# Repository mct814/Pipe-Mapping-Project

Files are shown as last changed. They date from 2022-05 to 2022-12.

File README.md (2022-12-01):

# Pipe-Mapping-Project

## Executive Summary
The problem that we wish to solve is a simple one. Underground PVC piping is often necessary to fix but difficult to locate. Methods currently exist for the detection of large industrial pipes, but there is a distinct lack of such technology for small, residential PVC
pipes. This project proposes a new way of mapping pipe networks by using a small probe to record positional data
while harmlessly traversing the pipe. The team’s objective is to create a probe based system to traverse and map variable sized underground pipe networks in 3D space, within an acceptable margin of error. While developing a mechanical pipe traversal method for the probe is part of this project, the primary goal consists of setting up the base technology for 3D mapping and real time information collection inside of 2"-4" PVC pipe.

## Current Version Capabilities
The current version of our design is still in the testing phase. While we have developed a functional testing system including a probe casing, pulley system and PVC network our current probe cannot fit inside the PVC pipe. The probe is using an arduino nano to pole data points and connect to the laptop which runs the mapping software. This probe can collect data while being powered by a set of 3 AA batteries and transmit said data to the PC. We have designed an improved system that would fit inside the 2" pipe but we have not yet implemented it. Our current mapping software can get data points within a relativiely similar shape to the physical path but still has a large margin of error. Further develpment of the mapping software is required to get within our original specification of 1" margin of error.

## Salient Outcomes
Our main successes came in the form of the mechanical testing system shown below and the preliminary maps created during testing.
* [Mechanical Testing](https://youtube.com/shorts/g99_hG3kM2Y?feature=share)

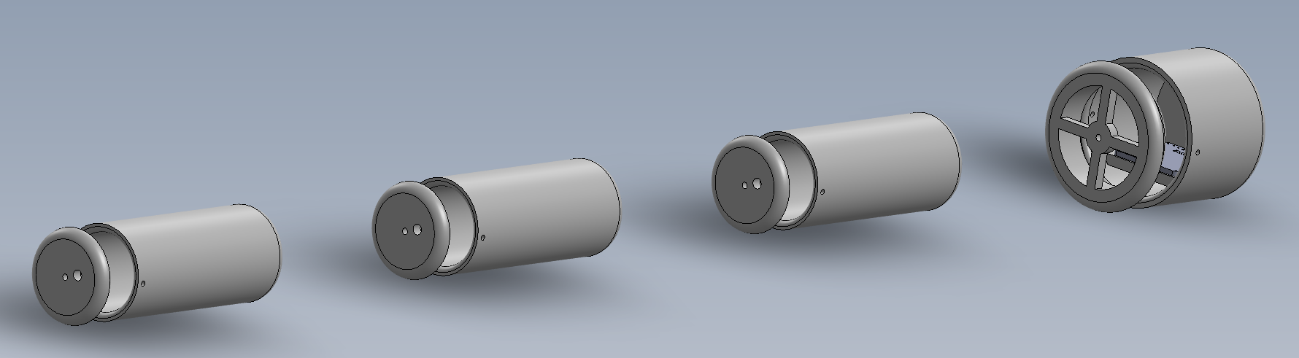
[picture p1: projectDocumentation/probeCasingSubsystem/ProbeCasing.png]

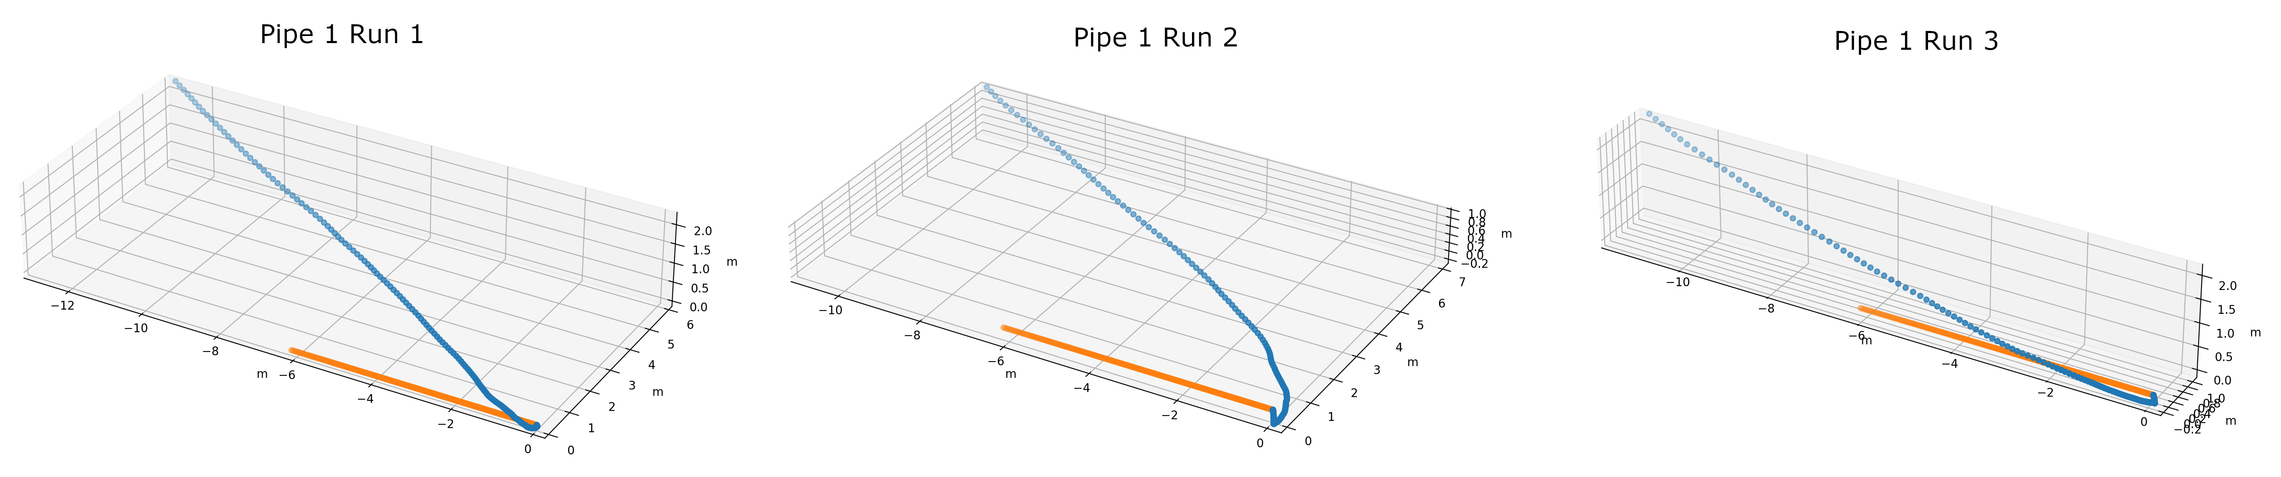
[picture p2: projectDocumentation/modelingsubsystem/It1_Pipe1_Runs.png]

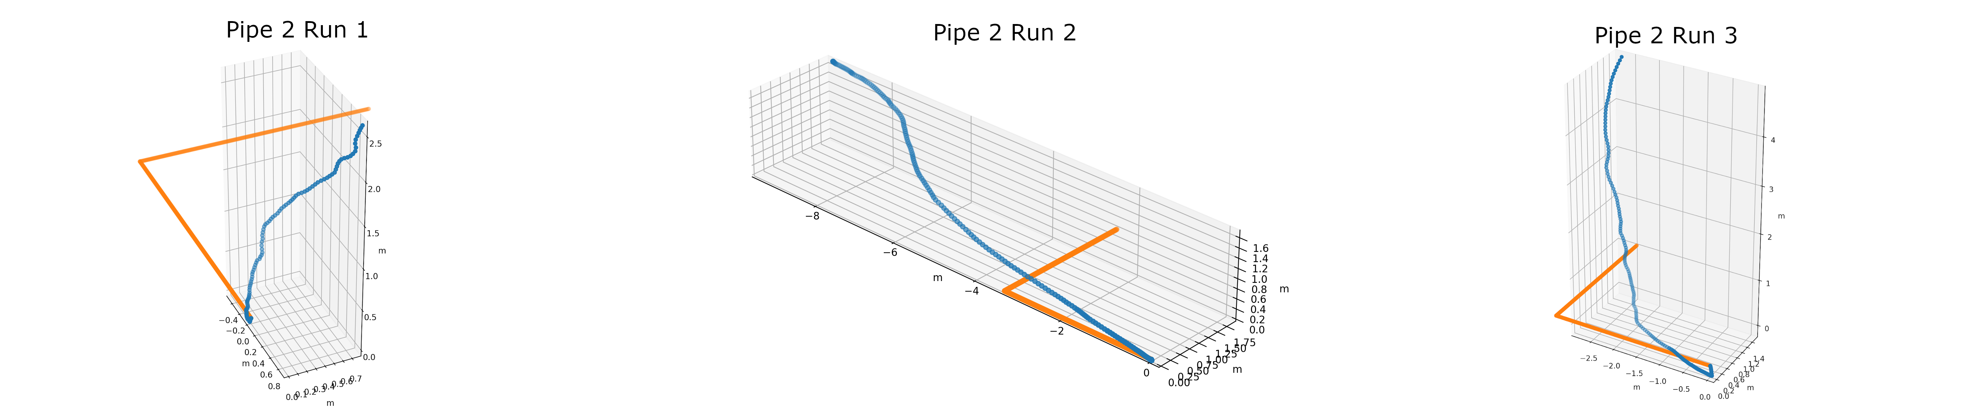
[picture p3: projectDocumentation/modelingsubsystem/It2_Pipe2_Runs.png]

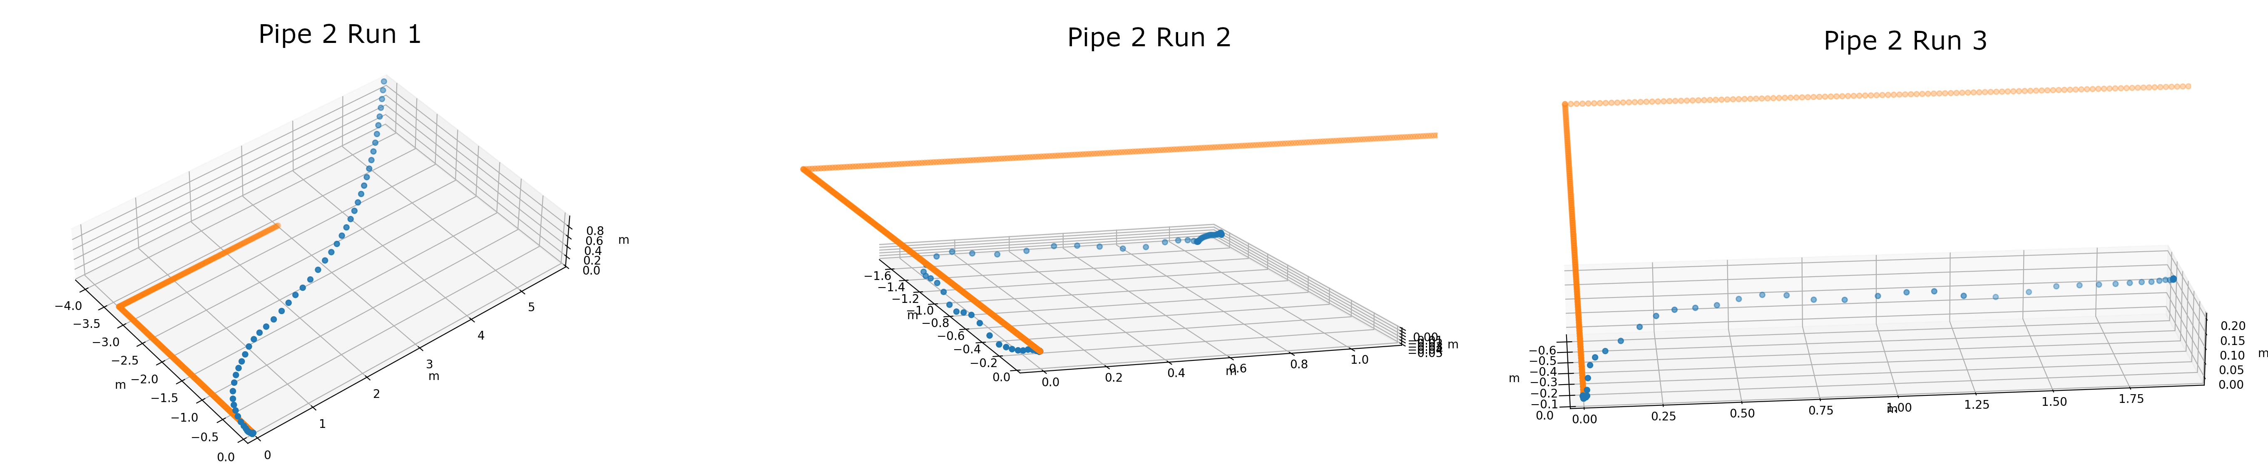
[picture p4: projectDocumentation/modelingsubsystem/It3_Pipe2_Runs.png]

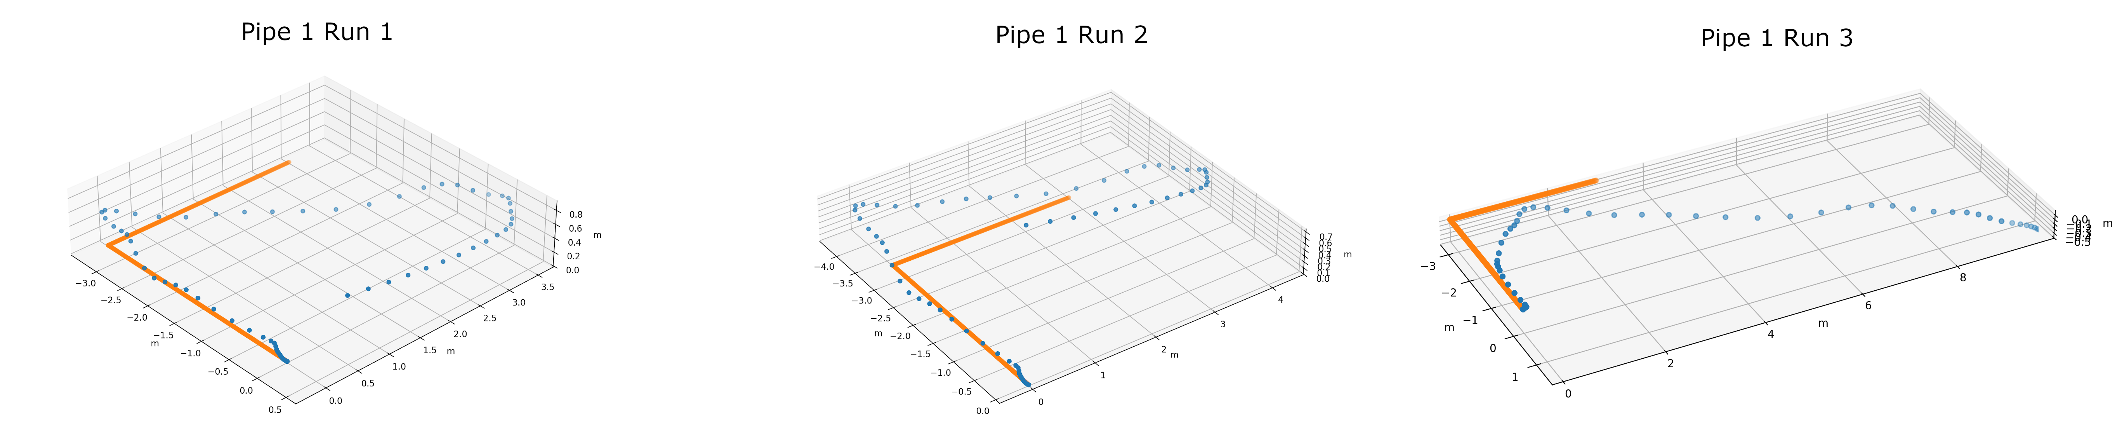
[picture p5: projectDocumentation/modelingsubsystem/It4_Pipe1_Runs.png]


## Testing Video
* [Probe Testing](https://youtube.com/shorts/lbEazcovoQ8?feature=share)

## Project Photos


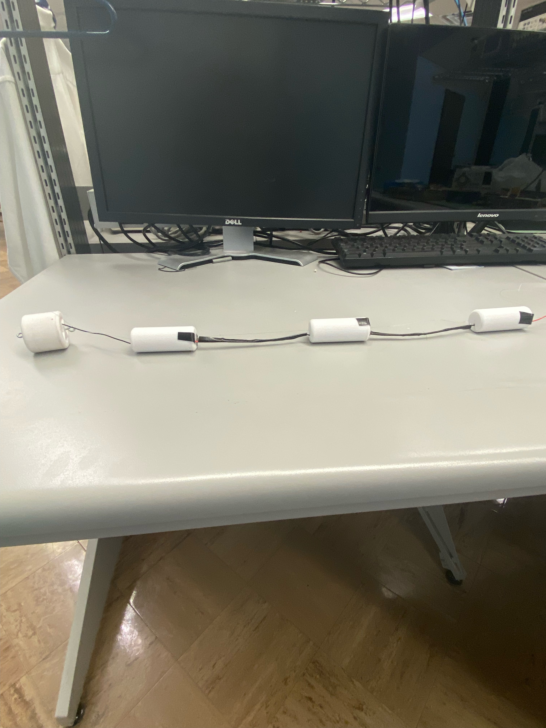
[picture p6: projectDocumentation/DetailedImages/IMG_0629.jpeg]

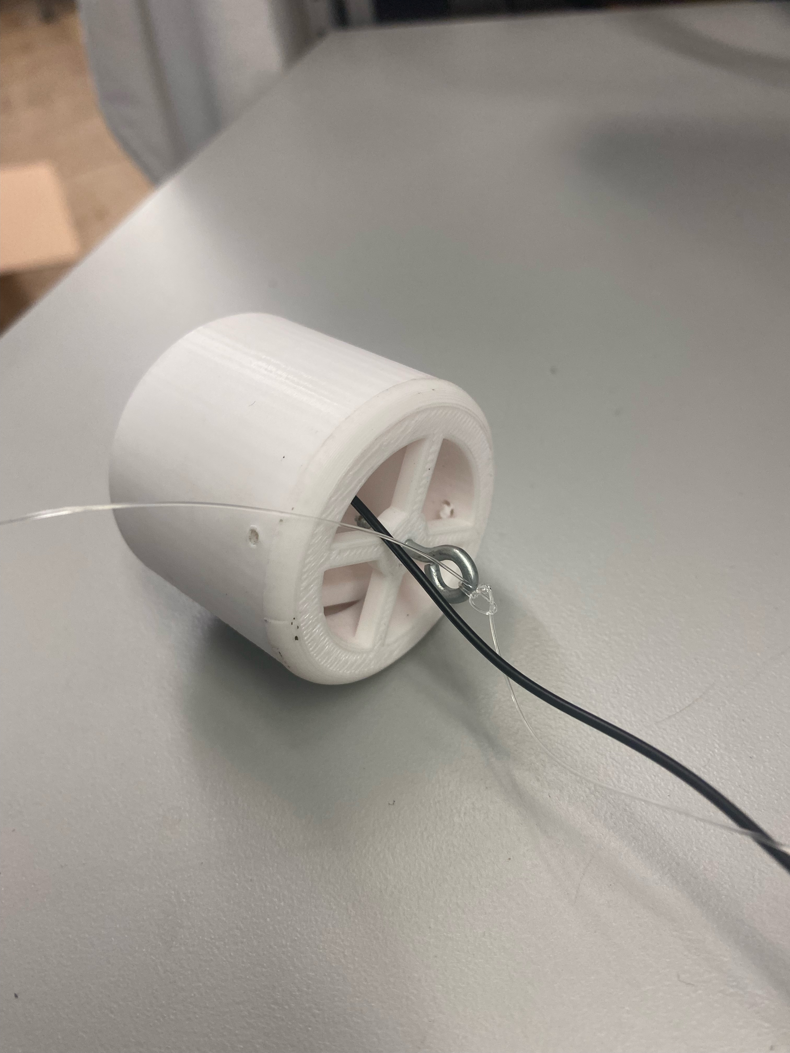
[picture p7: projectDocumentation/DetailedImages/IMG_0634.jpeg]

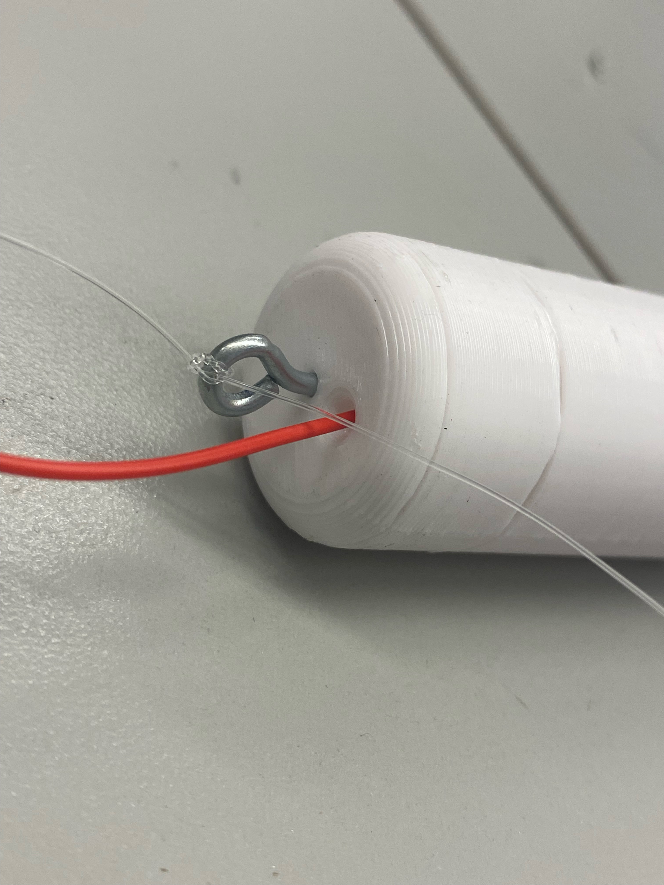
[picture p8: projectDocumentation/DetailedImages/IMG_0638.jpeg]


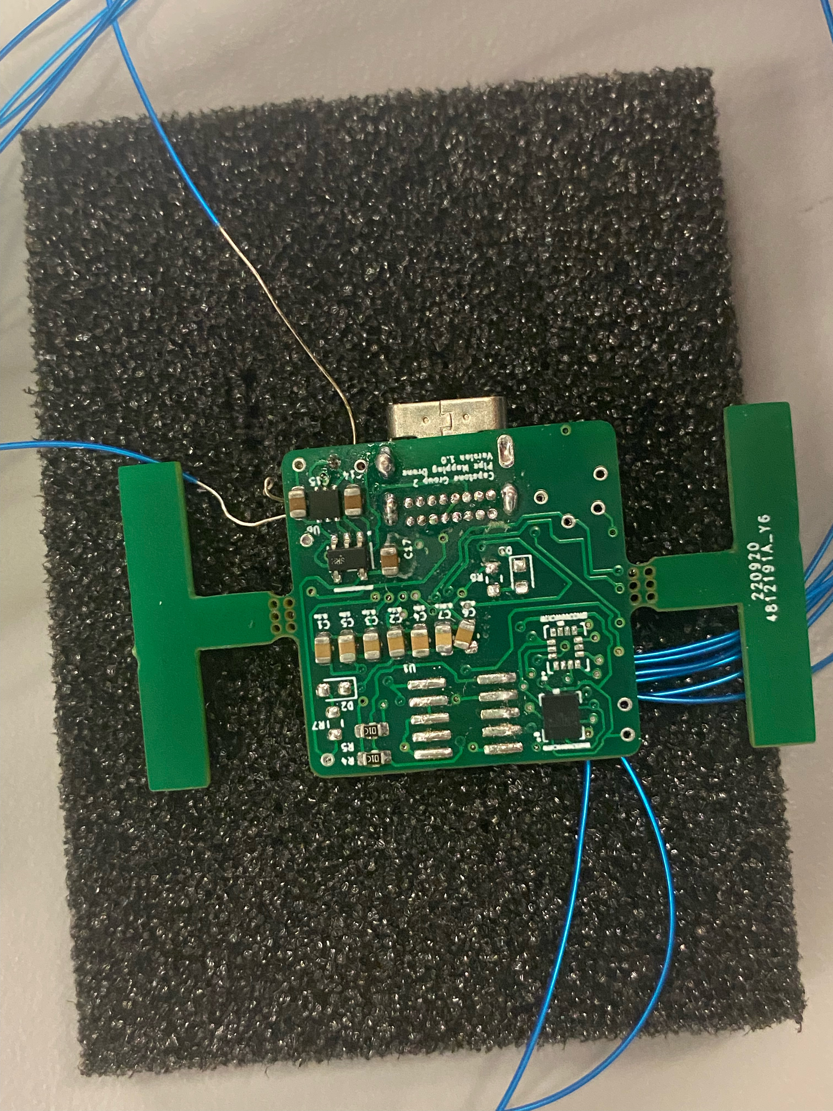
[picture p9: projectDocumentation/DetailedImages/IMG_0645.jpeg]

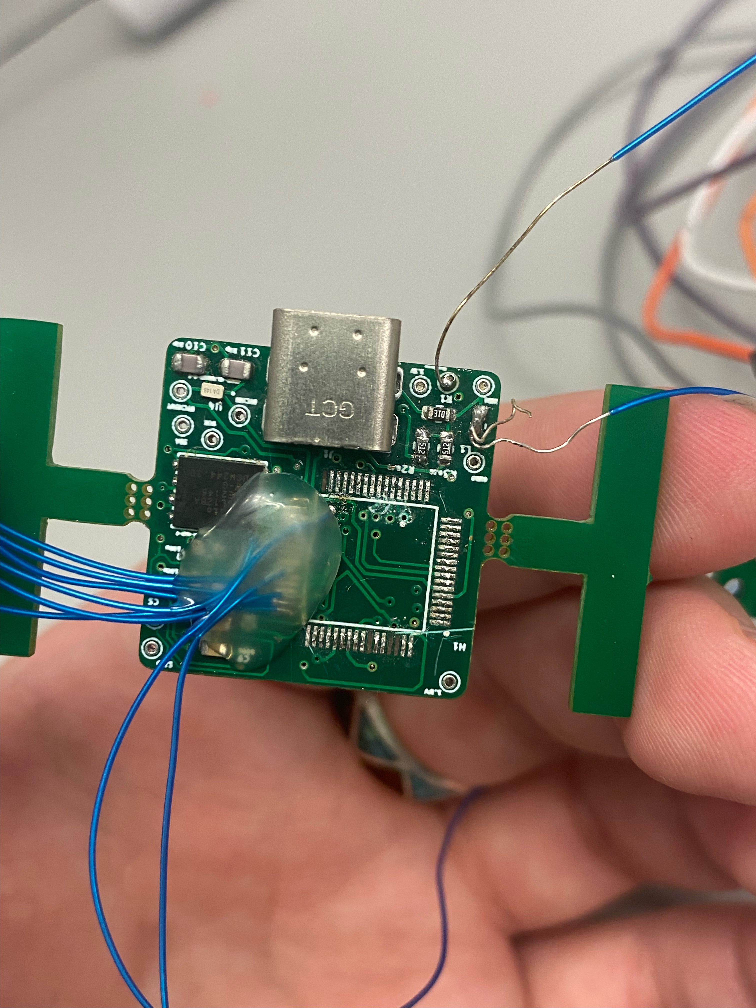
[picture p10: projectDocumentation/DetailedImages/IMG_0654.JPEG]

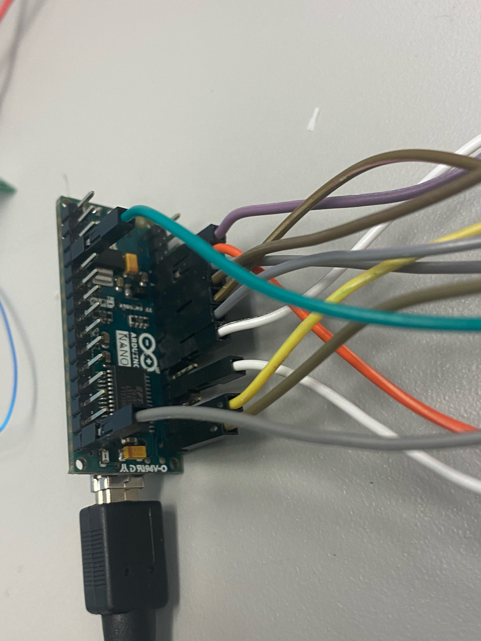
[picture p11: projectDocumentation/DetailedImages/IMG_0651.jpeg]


## About Us

### Developers

#### Adison Heathcott
I am a computer engineering senior at Tennessee Technological University. I am originally from Knoxville, TN and graduated from Bearden High School.

#### Ben Ask
I am a computer engineering senior at Tennessee Technological University. I am originally from Greensboro, NC and graduated from Ravenwood High School.

#### Caleb Thorne
I am an electrical engineering senior at Tennessee Technological University. I am originally from Pulaski, TN and graduated from Giles County High School.

#### Elizabeth Russell
I am an electrical engineering senior at Tennessee Technological University. I am originally from Tullahoma, TN and graduated from Family Christian Academy.

### Faculty Supervisor

#### Jesse Roberts

### Customer

#### Pipe locating services

## Description of Repository
The main file of the repository contains the lisence, readme, planned software file, reports folder, and project documentation folder. Inside of the reports folder are the original project proposal, the design phase 1 document, and the final report. Inside the project documentation folder is the bill of materials, project schematic and the folders for each of the subsystems that have been designed. Each of the subsystem folders contains schematics and readme descriptions of the design process.

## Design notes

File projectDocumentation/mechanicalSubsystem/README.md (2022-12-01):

# Mechanical Subsystem

## Mechanical Schematic
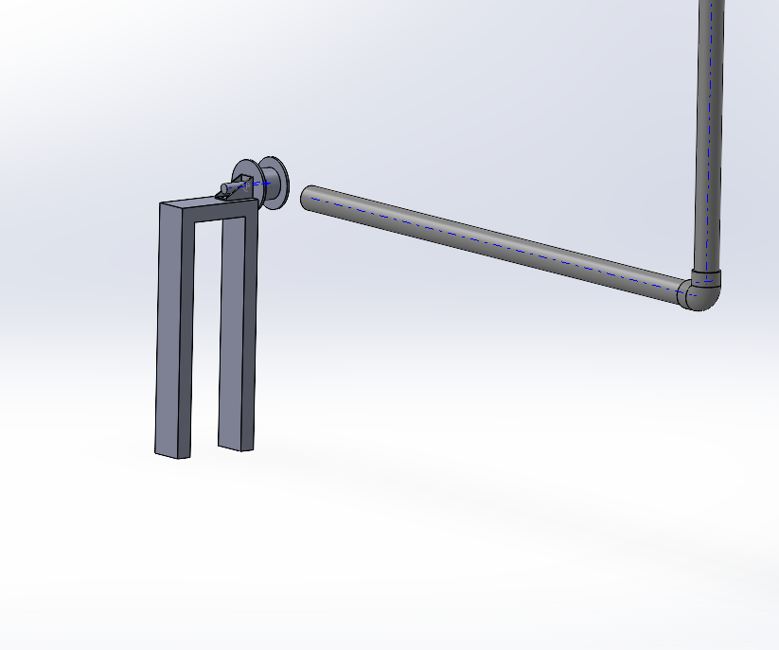
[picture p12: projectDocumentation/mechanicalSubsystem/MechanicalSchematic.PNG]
Mechanical Schematic


## Overall Design
The entire system is modeled below including the motor, motor bracket (3D printed),
motor stand (2x4 lumber), spool (3D printed), fishline, PVC pipe, and PVC 90 connectors.
The goal is to use this system to get our probe from one end of the pipe to the other. 
This will be achieved by hooking fishline into the grooves of the spool (described further in spool details) 
and attaching that to the probe which is discussed further below. Then the motor on either end of the pipe 
will turn at identical speeds to allow the probe to traverse the pipe at a consistent and controlled speed. 
The PVC network shown in the model is a rough image of what an actual test network may look like; more than 
likely the networks we make will be able to free stand from the ground up to the height of the motor stands 
with most of the PVC laid on the ground. We plan on using a couple of differently shaped pipe networks 
(reusing the same pipe) if possible which will be chosen at the time of testing starting with simple and becoming more complex.

## Motor
#### Component
47:1 Metal Gearmotor 12V with 48 CPR Encoder
* [Product Link](https://www.pololu.com/product/4865)

#### Relevant Specs
* Brushed DC
* Operates at 0.63 N-m of Torque
* Operates at 170 RPM

#### Analysis
* The torque needed was calculated based on a 1lb probe and 30ft of fishline with a 5 inch spool. 
Our probe is likely to be far lighter than 1lb which means torque calculation will be higher than 
what we actually need. Our spool is only 3 inches in diameter which means we will actually need less 
torque than what is calculated. Another aspect of the calculation is friction coefficient; I decided 
to use the friction coefficient of plastic on plastic which should be as high or higher than fishing 
line on PVC. This means again that the final torque calculated will be as high or higher than what we 
actually need. The calculations below first find the friction force of the fishline on the PVC and 
then the force needed to pull a 1lb probe. Then these forces are added together to get the total force 
needed which is then used to calculate torque. The final calculated torque needed to pull a 1lb probe 
through 30ft of PVC with a 5 in spool is about 0.0577 N-m. Therefore I have chosen a motor that produces 
up to 0.62762 N-m which is more than 10x the required minimum torque.

* The RPM requirement was calculated based on a 3 inch spool which is equal to the one we will be 
using and a probe linear velocity of 1 ft/sec. The calculations below convert linear velocity to angular 
velocity and then angular velocity into RPM based on our spool radius of 1.5 in. It was found that the 
motor needs to reach at least 76.39 RPM. Therefore I have chosen a motor that can reach 170 RPM which is 
over twice the calculated speed needed for the probe to travel at the required velocity.

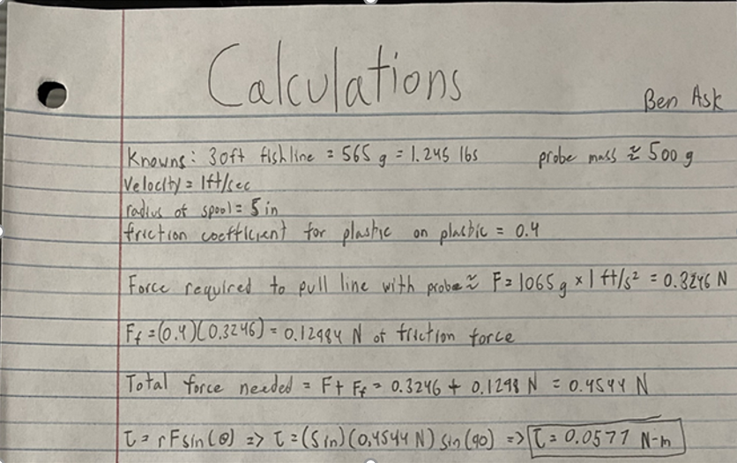
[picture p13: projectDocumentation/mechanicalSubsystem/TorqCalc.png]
TorqueCalculations

RPMCalculations

## Motor Mount
#### Component
Custom Motor Mount
* [Design Link](MotorMount.SLDPRT)

#### Relevant Specs
* Custom built to fit the motor chosen which is 25mm in diameter with 2 3mm mounting screws.
* Can be easily screwed into a 2x4 stand like the one in the schematic.

#### Analysis
* [Design Link](MotorMount.SLDPRT) 

## Spool
#### Component
Custom Spool
* [Design Link1](SpoolPt1.SLDPRT)
* [Design Link2](SpoolPt2.SLDPRT)

#### Relevant Specs
* Custom built to fit the motor shaft 4 mm diameter with 0.5 mm key groove.
* 3 inch radius with 5 inch radius walls to keep the fishline spooled without slipping.
* Designed in two parts so that it will be 3D printable.

#### Analysis
* [Design Link1](SpoolPt1.SLDPRT)
* [Design Link2](SpoolPt2.SLDPRT)

## Fishline
#### Component
Clear Fishing Wire
* [Product Link](https://tinyurl.com/y567u27d)

#### Relevant Specs
* 656 Ft of line
* 43 lb Test
* Diameter 0.45 mm 

#### Analysis
* This line will work for our system because our pipe network will only be 30 ft meaning that the maximum 
amount of line we will need is 60 ft. It also has 43 lb test which means that it will be more than strong
enough to pull a 1lb probe through our PVC network.

## PVC
#### Component
2" PVC Pipe
* [Product Link](https://www.lowes.com/pd/Charlotte-Pipe-2-in-dia-x-20-ft-L-280-PSI-PVC-Pipe/3133053)

#### Relevant Specs
* 2" diameter
* 20 ft long

#### Analysis
* This pipe is the industry standard and is within our goal pipe diameter of 1"-4".

## PVC 90s
#### Component
2" PVC 90 degree connectors
* [Product Link](https://tinyurl.com/33px97bh)

#### Relevant Specs
* 2" diameter

#### Analysis
* This 90 degree connector is compatible with the 2" PVC pipe we have chosen for our testing setup.

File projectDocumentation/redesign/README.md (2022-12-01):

# Redesign

The redesigned PCB is listed under the pcbSubsystem folder. 

## Signoff

This signoff is for the redesign of the pipe mapping drone. It includes the PCB, 2 LDOs, and a new memory chip. 

Components 

5V LDO (link here) 

1.8V LDO (link here) 

Memory (link here) 

GPIO Jumper (link here) 

Each of the components are shown to fit our design and our constraints In previous sign off requests. The 5V LDO is identical to the 1.8V LDO but the output voltage is changed to be able to power the Arduino. 

The new PCB does not meet our previous constraints listed in the previous design documents, however, it does fit the new constraints and will fit on top of the Arduino. We are printing a new casing to fit the arduino as well.  

5V LDO constraints: 

Power constraint 

The LDO is rated on the datasheet to be able to supply an adequate amount of power to the Arduino nano and the 3V LDO.  

The remaining analysis is shown in the image at the bottom of the page. 

PCB constraints: 

Size constraint 

The PCB must be 43.2 mm in length and 18 mm in width. This new PCB design fits this constraint. 

The PCB must fit the Arduino Nano GPIO pins. This new PCB uses the Arduino Nano sizing schematic, and the Eagle files to check against, to ensure that the GPIO pin holes are in the correct location. 

Power constraint 

The PCB has the soldering points to be able to connect to the battery and is connected to the Arduino 5V and GND pins, after the LDO, to be able to power the Arduino as well. 

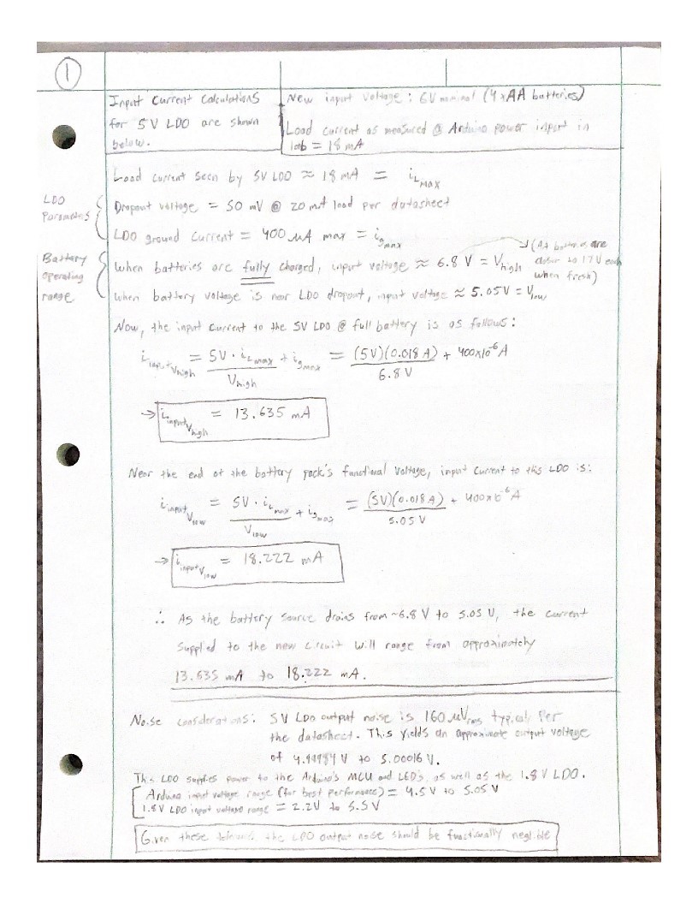
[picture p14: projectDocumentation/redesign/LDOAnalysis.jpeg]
LDOAnalysis


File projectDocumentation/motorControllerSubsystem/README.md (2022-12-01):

# Motor Controller Subsystem

## Overall Design
The entire recommended system setup (from the user manual) is modeled below with the motor controller, power supply (battery), and laptop connections shown.

## Motor Controller Schematic
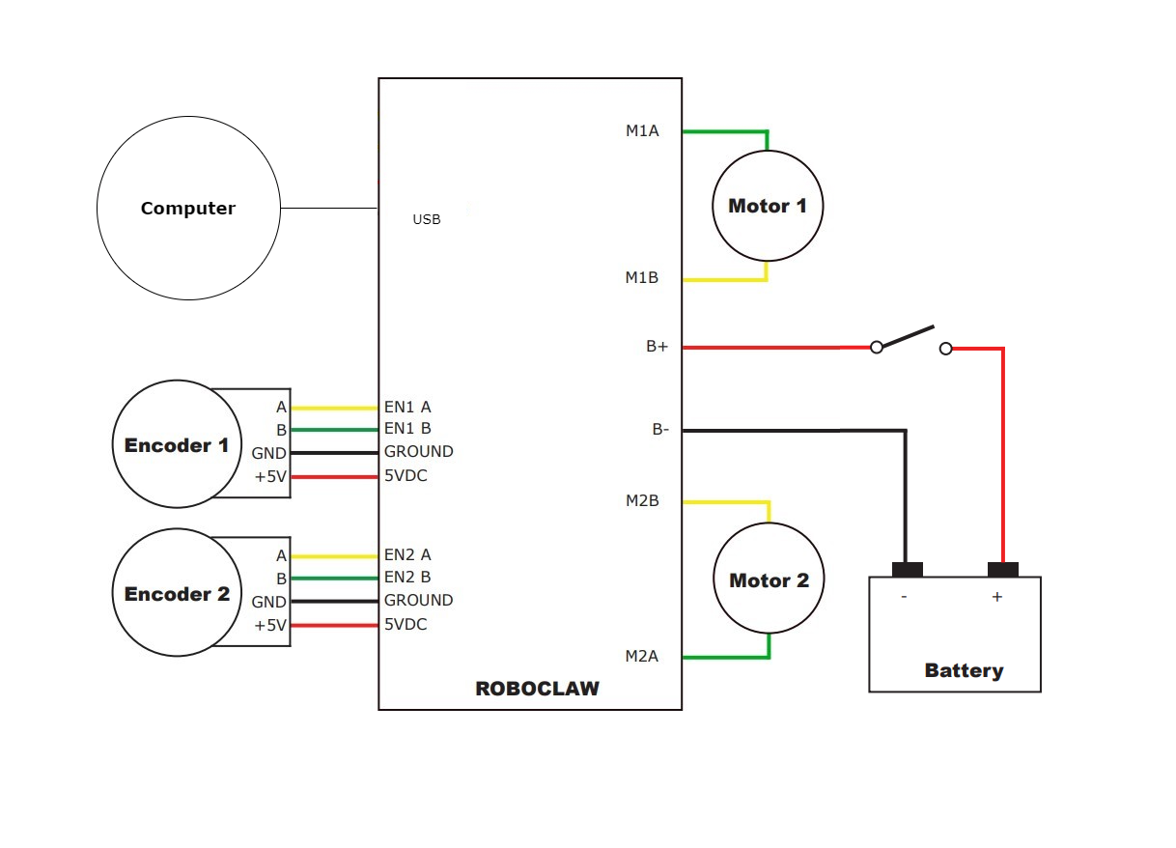
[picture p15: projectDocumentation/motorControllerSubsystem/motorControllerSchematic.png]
Motor Controller


## Motor Controller
#### Component
Roboclaw 2x7a Motor Controller
* [Product Link](https://www.basicmicro.com/Roboclaw-2x7A-Motor-Controller_p_55.html)

#### Relevant Specs
* Compatible with 2 brushed DC motors
* Operates up to 34 V and 15 Amps

#### Analysis
* 	1. Compatible with 2 Brushed DC motors:
	This motor controller is capable of controlling two brushed DC motors as shown in the figure taken from the datasheet above. This system also has a setting for running them in sync with each other as a part of the compatible software (Motion Studio) shown below.
	2. Meets or exceeds the stall current of the motor:
	This motor controller is designed to control two motors up to 34V 7.5 Amps continuous and 34V 15 Amps peak per channel which is well above the 12V 1.8 Amp stall current of each motor. These values were taken from the datasheets of both the motor and motor controller.
	3. Velocity Accuracy, and Variability:
	This controller can be controlled via USB (from data sheet shown above) which eliminates the need for an Arduino or Rasberry Pi for easy velocity control, and is compatible with quadrature encoders as stated in the datasheet which will allow for accurate velocity control regardless of load changes which are expected to occur during our testing. We said in the proposal that we wanted to be able to accurately read data at 1 ft/sec and this controller will allow us to accurately test different probe speeds and how they affect the data collection of the probe by setting a chosen velocity in the settings menu in Motion Studio. Motion Studio also includes the ability to see a real time graph of the velocity changes over time as seen below. The velocity requirement was calculated based on a 3 inch spool which is equal to the one we will be using and a probe linear velocity of 1 ft/sec (calculations in the mechanical subsystem signoff). It was found that the motor needs to reach at least 76.39 RPM. Therefore I have chosen a motor that can reach 170 RPM which is over twice the calculated speed needed for the probe to travel at the required velocity, because this controller provides adequate power to the chosen motor we can deduce that the speed minimum of 1 ft/sec will be easily reached with this controller.

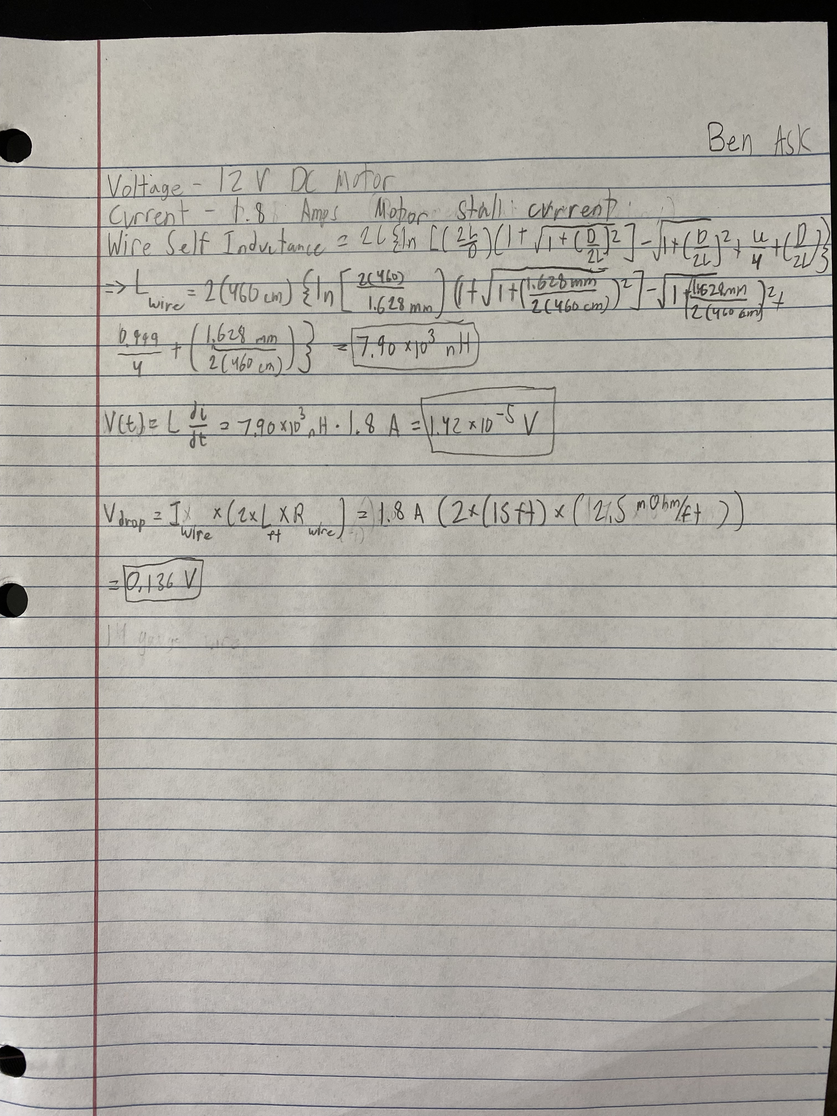
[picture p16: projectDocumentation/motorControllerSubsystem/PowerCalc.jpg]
Power Calculations


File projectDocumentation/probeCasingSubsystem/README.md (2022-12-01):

# Probe Casing Subsystem

## Probe Casing Schematic

Probe Casing

## Overall Design
The probe casing system has been 3D modelled below. The larger cylinder is for the PCB and the smaller cylinders have each been custom designed to fit a battery holder  
(linked above). Holes have been put into each end of the casings one for the wires and one for the screw eyelets. The screw eyelet holes have been custom designed to fit 
the screw eyelets linked above. The casings will be connected together via fishline which will be tied between the casings so as to not put tension on the 
electrical wires. The casings will then be connected via fishline to the reeling system which will pull it through the PVC piping. Each of these casings can be 
3D printed in the iCube and used immediately. Because the PCB case is almost 2" in diameter it will not be able to fit in the 1" PVC pipe but should still 
easily fit in any PVC 2" and above which meets our requirement of 2"-4" PVC.

## PCB Casing
#### Component
Custom PCB Case
* [Design Link](PCB Carrier.SLDPRT)

#### Relevant Specs
* Custom fit to PCB at 1.727" diameter and 1.476" length

#### Analysis
* The PCB casing was made as a cylinder to minimize friction inside the pipe while having a flat interior setting in order to cradle the PCB with minimal jostling.  
The larger cylinder for the PCB is 1.476" in diameter which will easily fit the 1" wide PCB. Glue will be used to secure the PCB to the interior of the casing. 
The cap for the casing is easily secured and removed via set screws in the side of the casing allowing for easy removal of the cap for connection with the USB onboard 
the PCB. The openings in the casing are for the batteries to be easily wired into the PCB when being set to use. There is also a screw eyelet hole that has been made 
custom to the one linked above. 

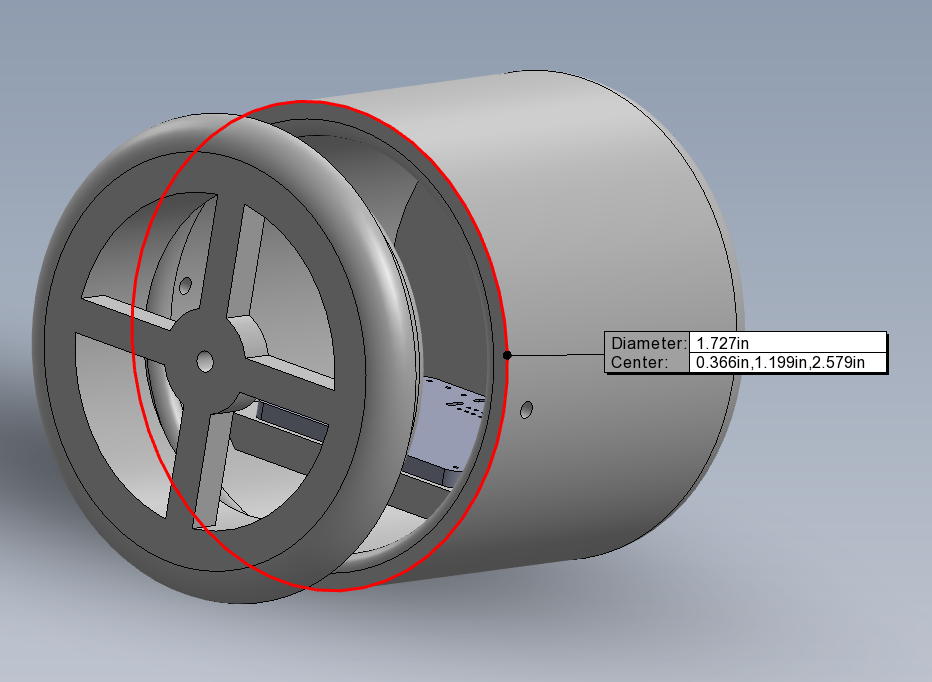
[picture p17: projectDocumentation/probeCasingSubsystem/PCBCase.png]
PCB Casing


## Battery Case
#### Component
Custom Battery Case
* [Design Link](Battery Carrier.SLDPRT)

#### Relevant Specs
* Custom built to fit the battery casings with 1.125" diameter and 2.248" length

#### Analysis
* The battery casing was made in the same fashion as the PCB casing to minimize friction inside the pipe while having a custom interior built for the battery holder linked above which is 2.248"x0.669"x0.539". The interior of the cylinder has a diameter of 0.875" which should easily fit the battery holder and it has an interior length of 2.5" which also fits the length of the battery holder. The cap for this casing will also be easily removable using a set screw in the side of the casing/cap to allow for easy replacement of batteries.

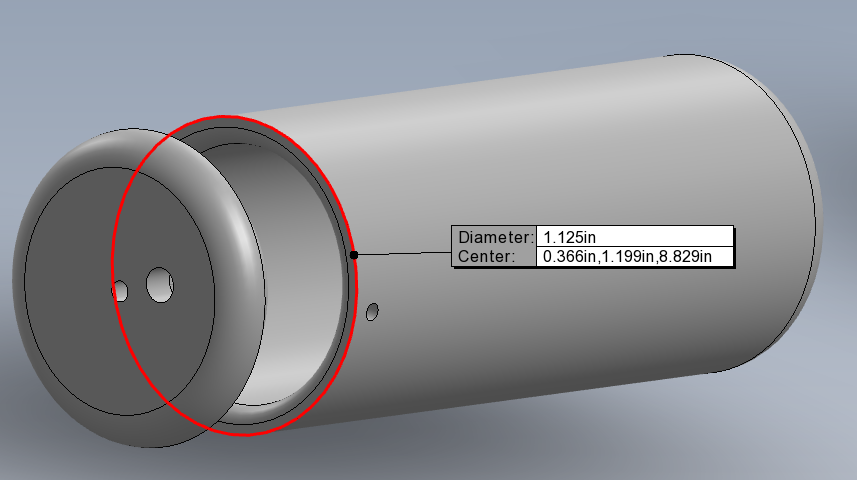
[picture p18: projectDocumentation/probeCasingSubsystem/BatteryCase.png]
Battery Casing


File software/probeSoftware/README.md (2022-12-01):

# Probe Software

## Functionality
The probe software should be loaded onto the arduino. This software is not written for the redesign, but for the current debug state of the previous board. If you use this software with the new board, you need to change the GPIO pin numbers.

Software states:
* Short pin D9 and D8 to read from the device
* Short pin D9 and D7 to record data on the device

The software does the following.
* Setup the Serial communication (57600).
* Setup the IMU
    * Set the accelerometer and gyroscope poll speed to 52 Hz.
    * Set the FIFO to FIFO mode
    * Set the FIFO to set the full bit at 128 bytes.
    * Enable the Timestamp counter
* Setup the Memory
    * Set pcConnected to true
    * Set pcConnected to false, and erase the memory if recording new data
* Program Loop
    * IF pcConnected is false
        * Get the number of entries in the fifo
        * Store the data in the fifo into memory one page at a time (The memory only supports writing a maximum of 256 bytes at a time)
    * IF pcConnected is true
        * Get the number of entries saved in memory
        * Read the information in on continuous read (supported by current memory chip)
        * Send the information to the pc through the USB cable 

## Dependecies
The only dependencies are the Arduino SoftwareSerial and SPI libraries.

## How to install / run
Load this software file into the arduino software and send it to the device.

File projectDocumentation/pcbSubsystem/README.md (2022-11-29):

# PCB Subsystem

## PCB Schematic
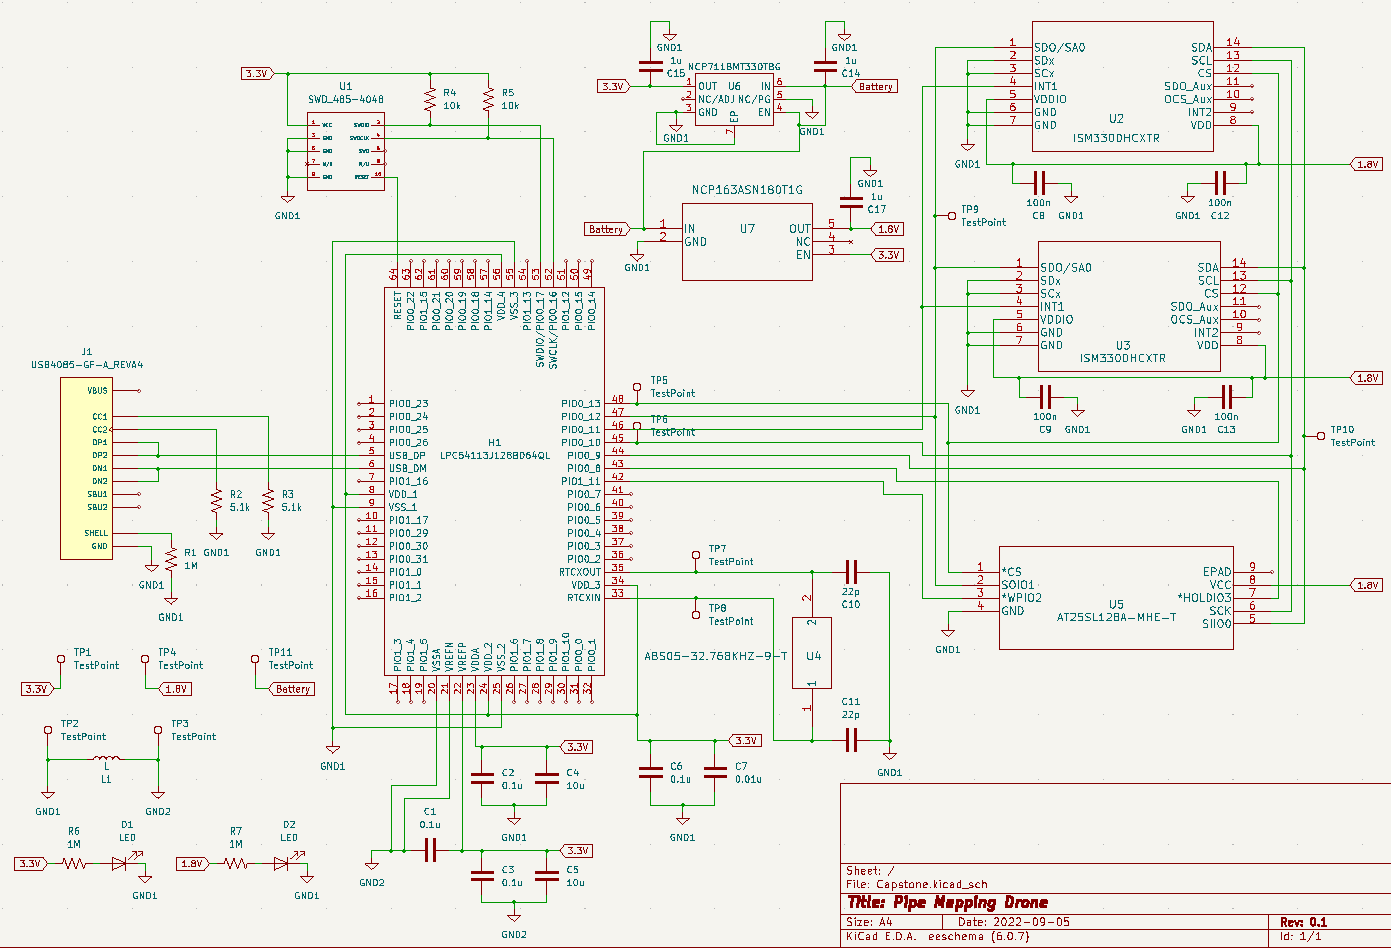
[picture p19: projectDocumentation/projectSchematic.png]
PCB Schematic


## KiCAD Files
KiCad files are supplied and can be loaded into KiCAD.

***CAUTION***
*The current design has errors. Look to the redesign for error corrections and a usable PCB*

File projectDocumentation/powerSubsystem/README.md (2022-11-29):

# Power Subsystem

## Power Subsystem Schematic
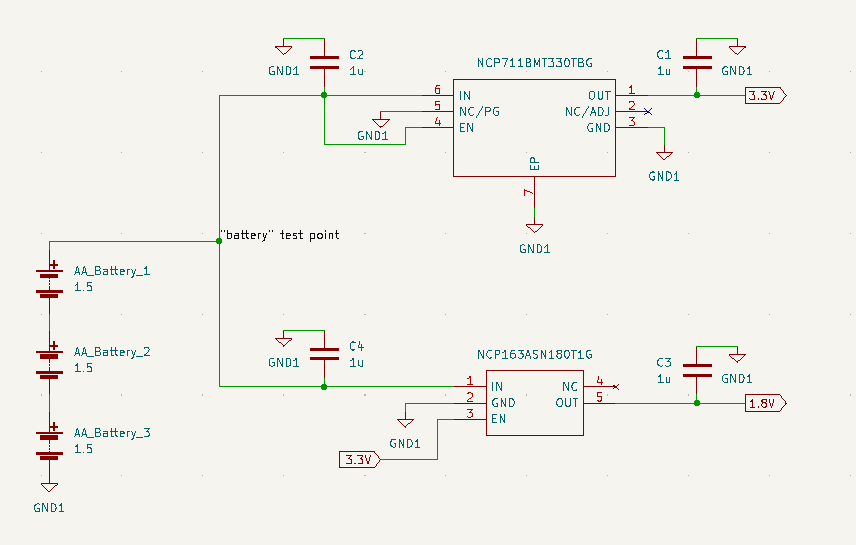
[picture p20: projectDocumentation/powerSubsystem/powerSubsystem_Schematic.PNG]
Power Subsystem Schematic


## LDOs
#### Components
NCP163ASN180T1G (1.8V LDO)
* [Mouser Link](https://www.mouser.com/ProductDetail/onsemi/NCP163ASN180T1G?qs=vLWxofP3U2z0o2tJM%252BNAYw%3D%3D) <br/>

NCP711BMT330TBG (3.3V LDO)
* [Mouser Link](https://www.mouser.com/ProductDetail/onsemi/NCP711BMT330TBG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)

#### Relevant Specs
* Low dropout voltage, suitable for battery
* Minimal output noise
* Small package sizes, which are necessary due to the size constraints of the pipe's inner diameter 

#### Analysis
The LDOs were chosen and verified to work based on these considerations
* Output noise analysis
    * The LDO output voltage noise was calculated using the "Output Voltage Noise" parameters found in each LDO datasheet, and evaluated against each supplied subsystem's input . The output noise from these regulators was found to be functionally negligible, and should not impact system performance.
    * The calculations for the noise analysis are attached at the bottom of the README.
    
* Input Current Analysis
   * Another crucial step in designing the power subsystem was understanding how much current needed to be supplied by the batteries. In an attempt to ensure that we didn't underestimate the device's potential current draw, we based the calculations on each supplied subsystem's maximum current draw rather than each subsystem's nominal current draw. 
   * The calculations for the maximum current supplied to each LDO regulator are attached at bottom of the README.

* Battery Runtime Analysis
   * In our project proposal, we specified that the battery should be able to power the device long enough to map 5,000 feet of pipe before battery replacement was necessary. 
        <br/> * Given that our probe speed has been defined in our previous documents as 1 ft/s,  a total of 5,000 ft of pipe would take 5,000 seconds, or 83.33 minutes of runtime. 
       <br/>  * Alkaline AA batteries typically have a capacity rating between 2000-3000 mAh, with 2500-2850 mAh being a more common range when under 50 mA constant drain. To account for the case of lowest normal capacity, we'll assume the battery pack only has a capacity of 2000 mAh at <50 mA constant drain. 
        <br/> * Given a total maximum supplied current of around 17.76 mA, the potential battery life would generally be around: 2000mAh/17.76mA = 112.6 hours.
        <br/> * However, it should be noted that this estimation will vary depending on factors such as the specific discharge characteristics of a given battery, operating temperature, and actual load current, which will vary based on both device operations as well as battery voltage. For this device, we must also specifically account for the dropout voltage of the LDOs. The relevant dropout voltage we must consider is that of the 3.3V LDO, which is 355 mV maximum. In order for the LDO to supply a stable 3.3V to the MCU rail, the LDO input voltage will need to stay above roughly 3.655V. This means that the device may not function for the full life of the battery, but only up until each battery has dropped to around 1.22V. Given that alkaline AA batteries can often drop as low as 0.8V before they are totally discharged, it must be noted that the device will most likely stop working due to insufficient power before the batteries have been fully drained. 
        <br/> * For the sake of meeting our specifications however, it appears that this battery system will be more than capable of meeting our original runtime requrement of 5,000 ft worth of pipe, or 83.33 minutes, even assuming that the batteries will only be functional until the point that their total voltage is 3.665V. At a maximum total current drain of around 17.76 mA, the manufacturer discharge curves of a regular Duracell Coppertop AA battery indicate that their AA batteries could provide over 100 hours of service time by the time that they discharge to 1.22V. This runtime far exceeds our goal of roughly 1 hour and 23 minutes of runtime. 
    
## Output Noise Analysis
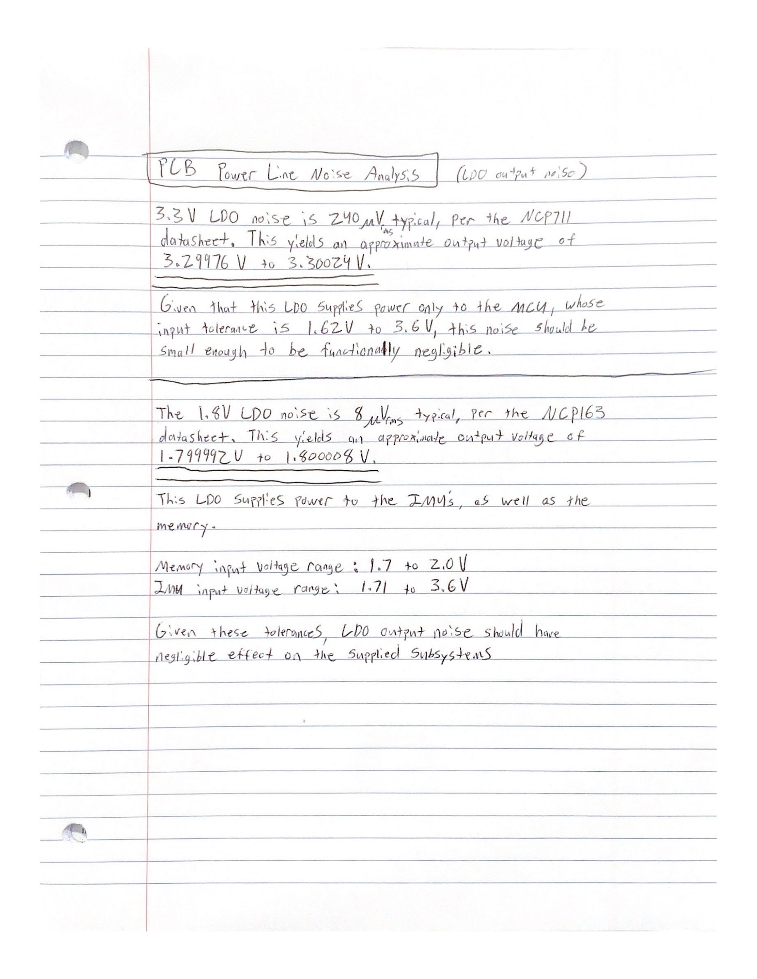
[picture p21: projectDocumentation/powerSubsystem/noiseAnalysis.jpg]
Output Noise Analysis


## 3.3V LDO Input Current Analysis
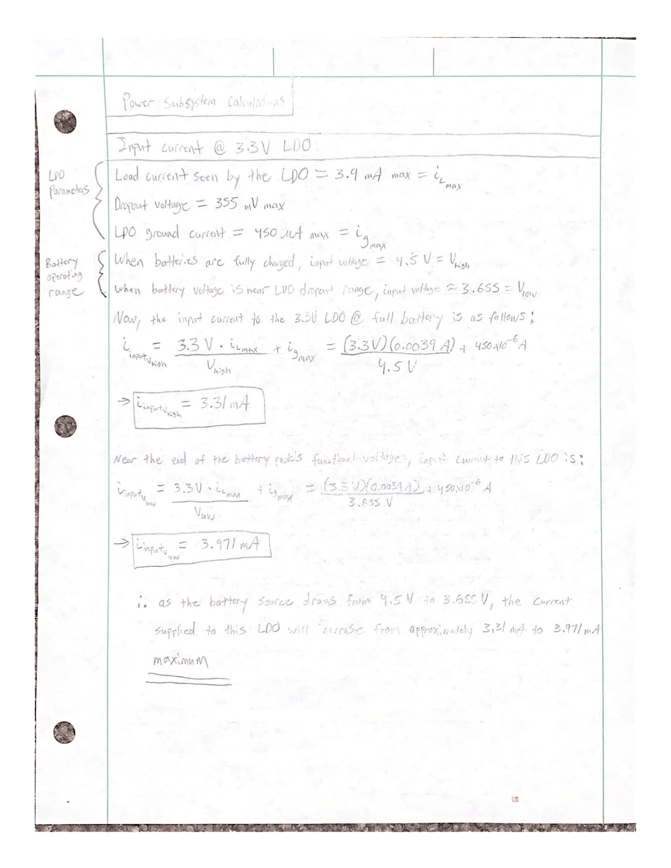
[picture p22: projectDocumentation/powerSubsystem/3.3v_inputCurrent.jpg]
3.3V LDO Input Current Calculations


## 1.8V LDO Input Current Analysis
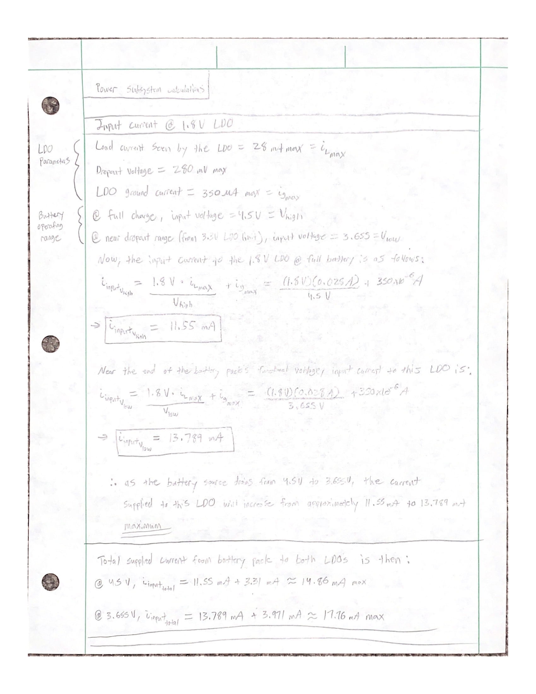
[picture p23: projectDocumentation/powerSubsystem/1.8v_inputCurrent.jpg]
1.8V LDO Input Current Calculations


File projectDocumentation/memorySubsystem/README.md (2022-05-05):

# Memory Subsystem

## Memory Schematic
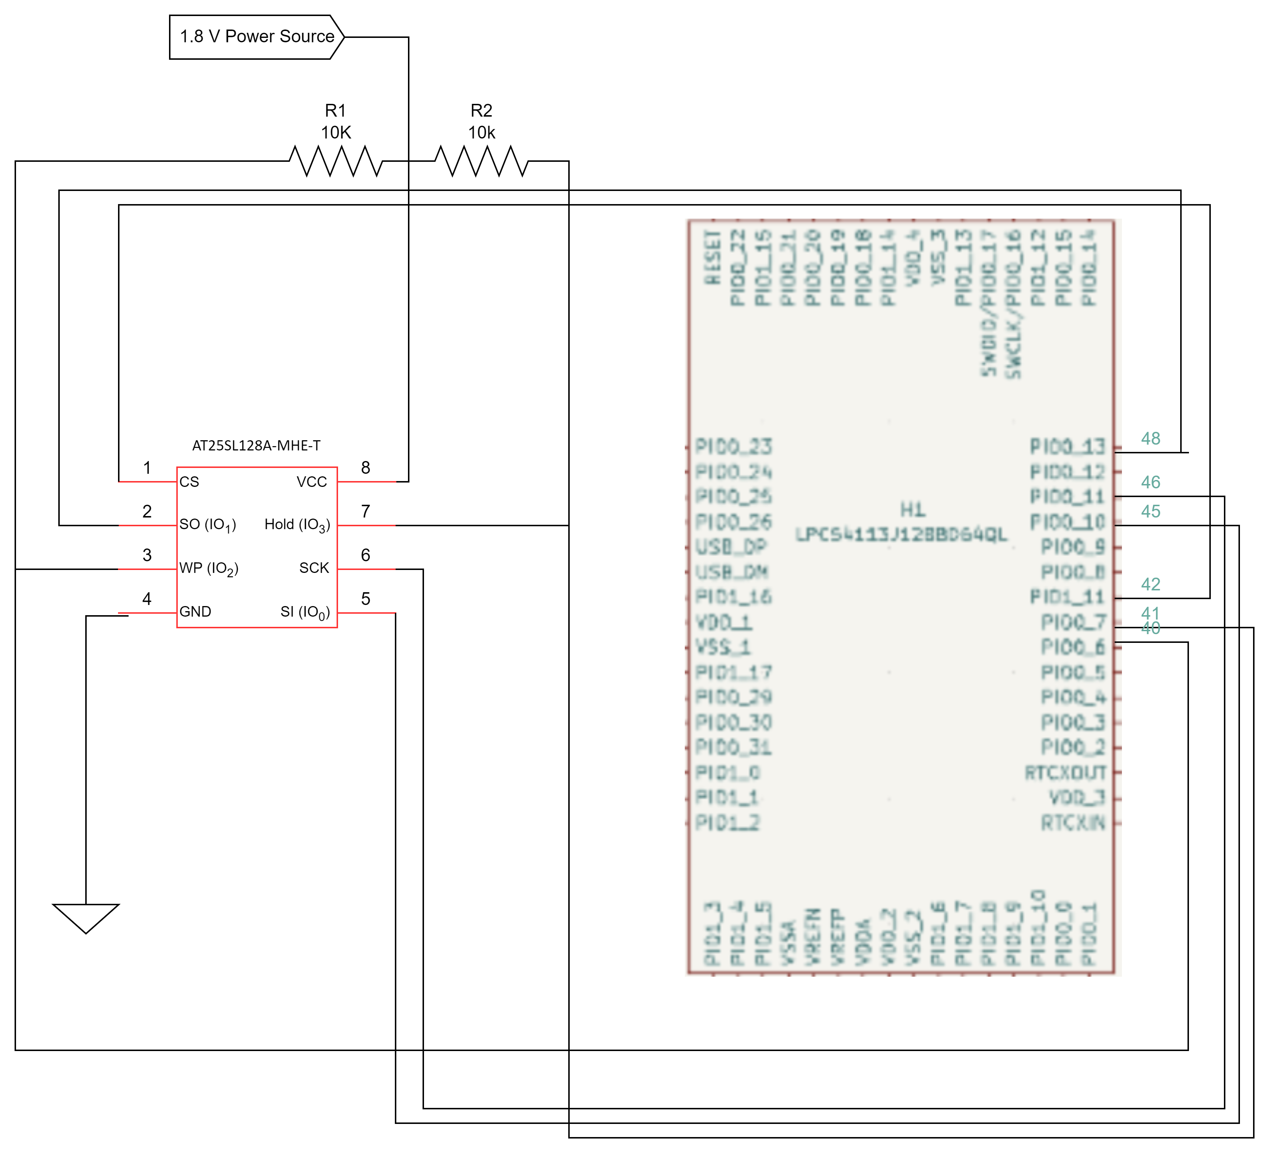
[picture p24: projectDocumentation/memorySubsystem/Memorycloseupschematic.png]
Memory Schematic


## Memory chip
#### Component
AT25SL128A-MHE-T
* [Digikey Link](https://www.digikey.com/en/products/detail/adesto-technologies/AT25SL128A-MHE-T/6827494)

#### Relevant Specs
* Operates up to 133Mhz
* SPI support
* Size of memory
* Size of package

#### Analysis
The device was chosen and verified to work based on these standards
* 133 MHz clock speed
    * This clock speed will be able to keep up with the microcontroller, as the speed I found when reading the microcontroller communication was aproximately 100 MHz.
* Capable of SPI communication
    * Memory needs SPI to communicate with the microcontroller, and this chip has standard, dual, and quad SPI operations.
* 128 Mb of FLASH memory
    * The chip can Read/Write up to 2 bytes per 150 microseconds of information, so can easily store all the data sent to it. The calculations that proved this are found below. 
      * These calculations are determining the number of samples (data points) taken by the system. There are two separate calculations, as our estimated pipe length will be between 20 and 40ft, on top of those calculations I calculated multiple sets of data, up to 6 sets per length of pipe, and for two separate speeds, 1ft/sec and 0.1ft/sec.
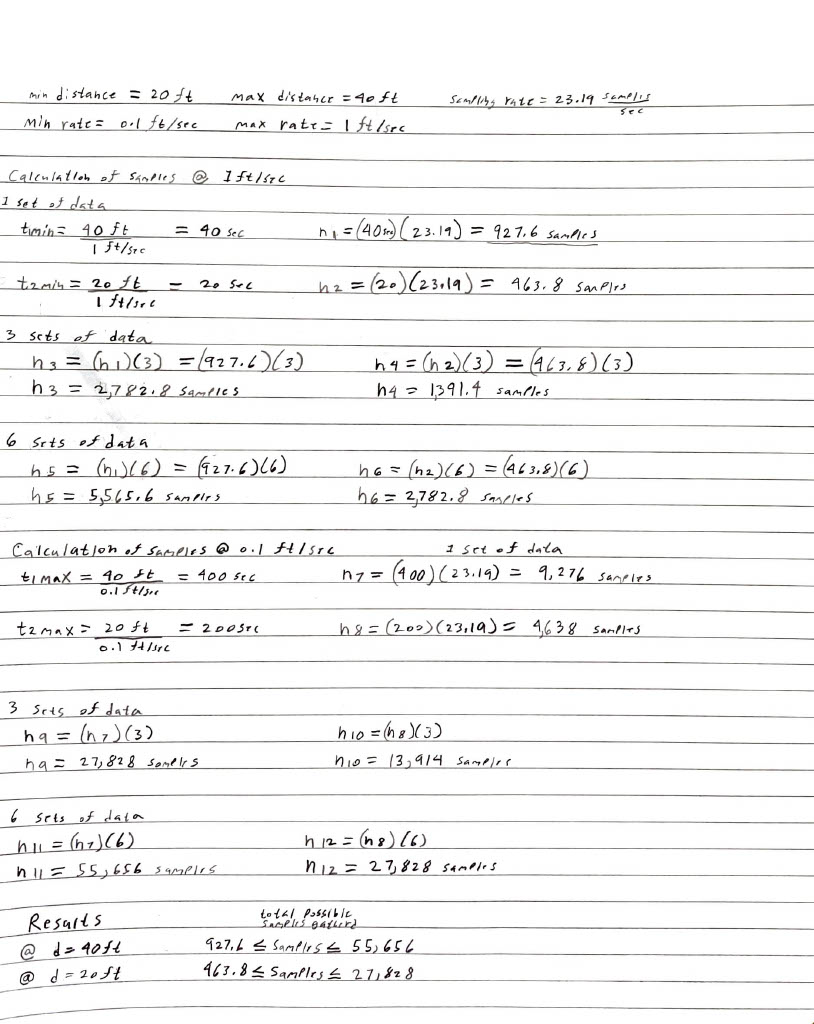
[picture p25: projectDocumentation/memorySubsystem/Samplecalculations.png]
Sample Calculations
        
      * These calculations are to determine that the memory size of the chip meets/exceeds the number of samples, as each sample is stored and sent in either in a single byte or two bytes. For the calculations I assumed each sample was stored and sent in two bytes so the estimated size required will be larger than what is needed, The maximum sample size was taken from Figure 1 calculations and multiplied by the number of bytes to obtain the bytes of memory required. this figure also shows the breakdown of how many bytes are in the chip, to easily compare whether the chosen storage size meets/exceeds expectations, and they do as the maximum number of bytes required are 111,312 bytes and the memory size is approximately 128,000,000 bytes. 
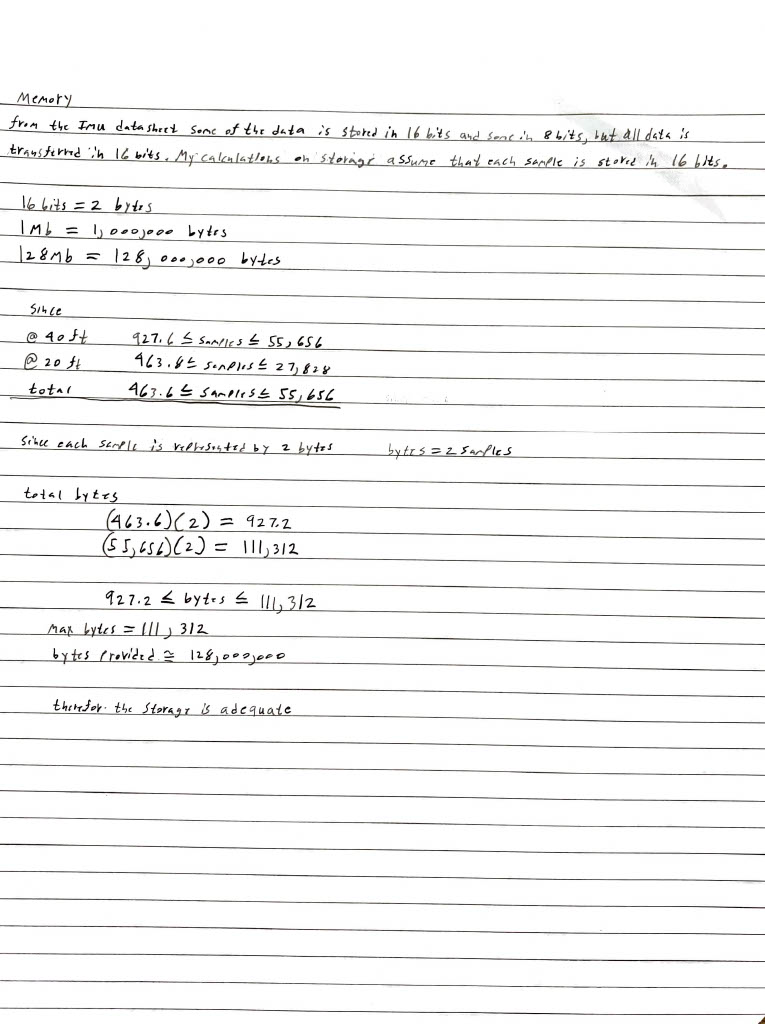
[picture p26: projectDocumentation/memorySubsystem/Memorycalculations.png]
Memory Calculations
     
* Package size of 5 x 6 x 0.6 mm
    * Since the size constraint for the hight is 1" the package size was one of the main constraints of the chip, as it is the size is the smallest found with the minimum storage capacity of 100Mb.

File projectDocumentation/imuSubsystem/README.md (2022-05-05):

# IMU Subsystem

## IMU Schematic
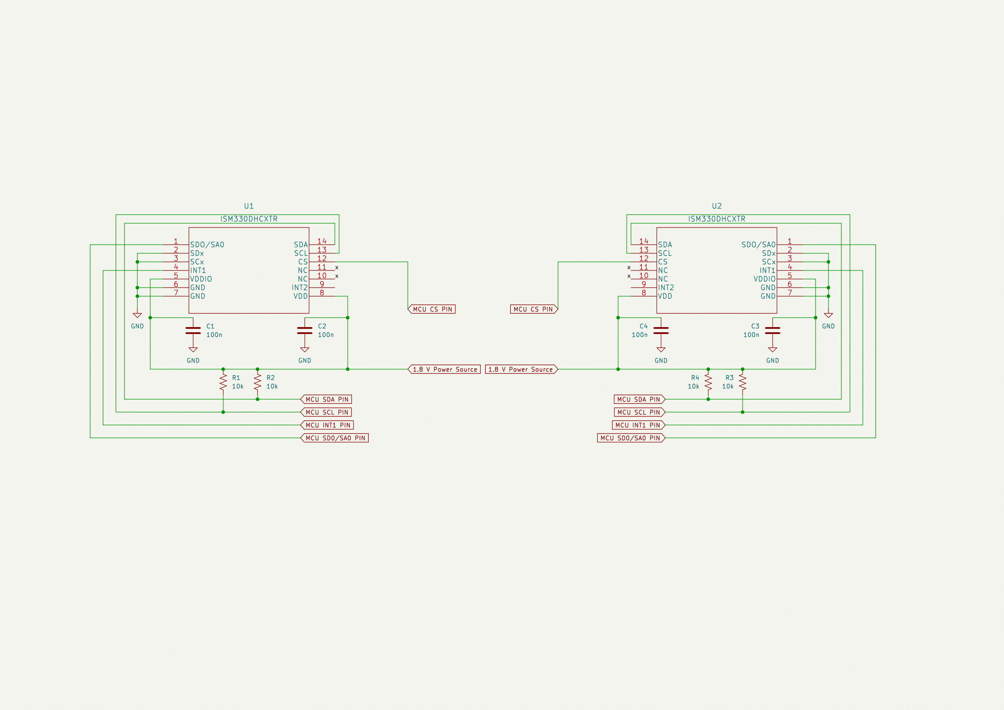
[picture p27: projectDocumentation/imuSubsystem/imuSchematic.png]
IMU Schematic


## IMUs
#### Component
ISM330DHCXTR
* [Digikey Link](https://www.digikey.com/en/products/detail/stmicroelectronics/ISM330DHCXTR/10409727)

#### Relevant Specs
* 6-axis accelerometer, 6-axis gyroscope, and temperature sensors
* SPI and I2C support
* Small package (LGA-14), which is necessary due to the size constraints of the pipe's inner diameter 

#### Analysis
The IMUs were chosen and verified to work based on these considerations
* General Sampling Rate Analysis
    * While the team did not initially specify a required sampling rate for the device, the device will need to be capable of sampling fast enough to ensure that positional data remains as accurate as possible. The calculations made for the required sampling frequency are shown below. The possible output data rates of the accelerometers range from 1.6 Hz to 6.67 kHz, while the output data rates of the gyroscopes range from 12.5 Hz to 6.67 kHz. Given that the physical mapping environment is relatively linear by nature, and the team plans to pull the probe through at a maximum rate of 1 foot per second, this range of sampling rates will be plenty high enough to obtain accurate mapping data.

* Worst Case Sampling Scenario (encountering short radius 90° angles at maximum traversal speed)
   * All 90° elbows referred to in the subsequent calculations are the SR (short radius) variety, as this will result in a shorter elbow arclength as opposed to LR (long radius) elbows. Note that LR elbows are the standard variety of pipe elbow, but in this interest of calculating a worst case sampling scenario, short radius elbows will be used in these calculations. 
   * The interior diameter of the pipe network is equal to 1" 
   * The probe will be pulled though the network at the maximum rate of 1 foot per second
   * The calculations for this scenario are attached at the bottom of the README
    
## Sampling Calculations
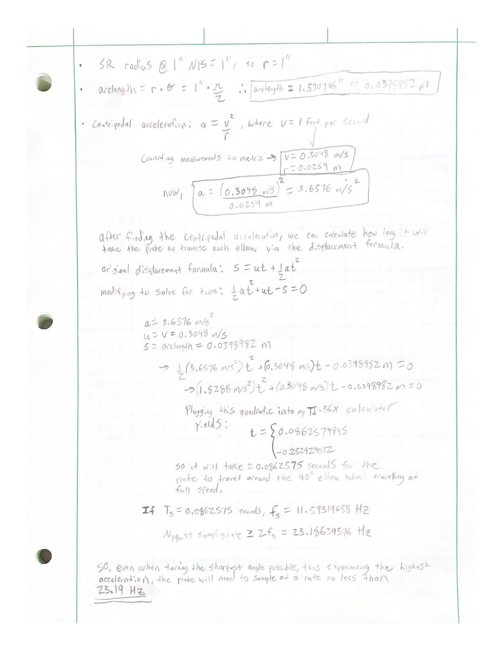
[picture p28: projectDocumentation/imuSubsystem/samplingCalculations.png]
Sampling Calculations


## Worst Case Scenario Sampling Calculations
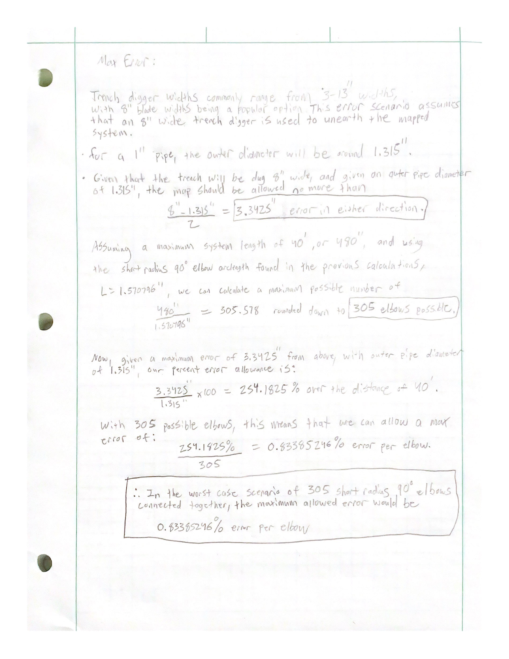
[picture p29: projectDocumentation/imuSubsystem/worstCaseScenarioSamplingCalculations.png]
Worst Case Scenario Sampling Calculations


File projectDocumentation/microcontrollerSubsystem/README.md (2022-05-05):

# Microcontroller Subsystem

## Microcontroller Schematic
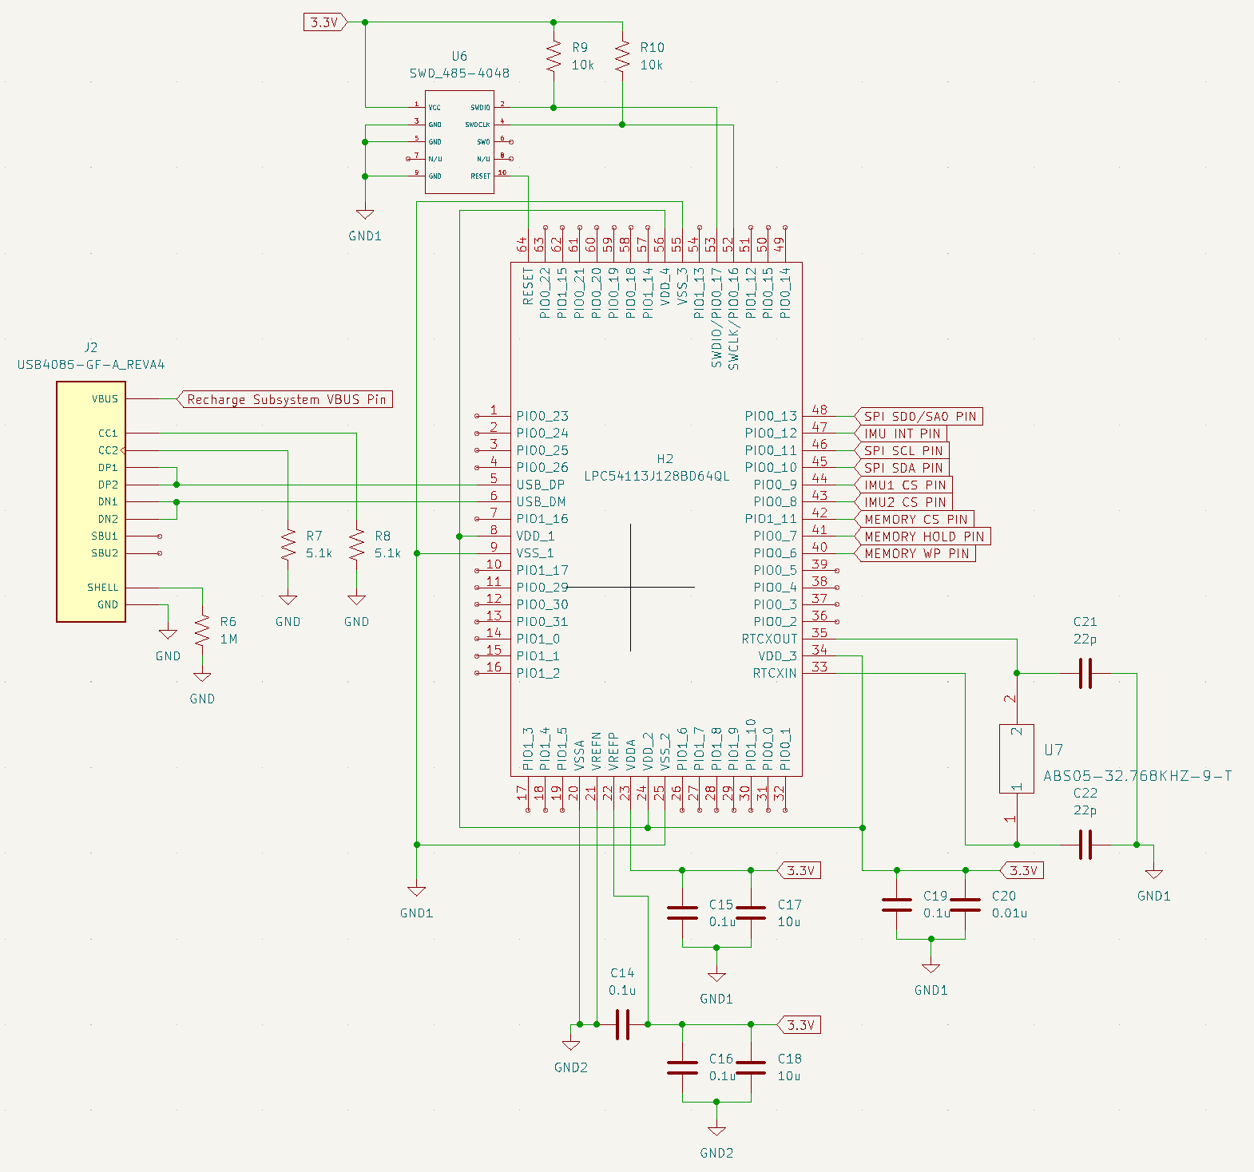
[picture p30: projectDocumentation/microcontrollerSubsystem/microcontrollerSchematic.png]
Microcontroller Schematic


## Microcontroller
#### Component
LPC54113J128BD64QL
* [Mouser Link](https://www.mouser.com/ProductDetail/NXP-Semiconductors/LPC54113J128BD64QL?qs=45Avz0nZxhtx28X6DfvU%252Bg%3D%3D)

#### Relevant Specs
* Dual Processor Cores operating at 150 MHz
* SPI, I2C, USART, and USB 2.0 support
* 48 GPIO pins

#### Analysis
The device was chosen and verified to work based on these standards
* Capable of SPI communication
    * Memory and the IMUs both need SPI to communicate.
* 32 bit device with 48 GPIO pins
    * The IMU data will be collected at 16 bits per sample so 32 bits will be more than enough to handle the IMU data and the memory size.
* Capable of USB communication
    * This chip has special pins built for USB communication which will make designing easier
* 150 MHz clock speed
    * The IMUs have the ability to store 3 KB (9 KB if compressed) of measurement data in a buffer. If the IMU is collecting 16 bit information at 104 Hz (which is the start testing frequency) it will have about 15 seconds before the buffer is filled and data is overwritten. SPI is capable of data rates up to 60 Mbps. This would allow us to set the clock to a KHz speed and pull the buffer data in about 1 second. The storage chip can also run at up to 60 MB/s. This would allow the chip to run at a low power clock speed and still be able to keep up with the recorded data. In summary, this chip has the necessary clock speed to handle and communicate modes to properly handle the data input rate.
* 192 KB SRAM
    * Each chip can output up to 9 KB of information from a full, fully compressed buffer. Even if the chip cannot immediately store the data it received there is more than enough memory to handle both IMUs. The only scenario in which we would have a problem is if there is an error sending data to the memory chip and we cannot offload any data during the entire process of the measurement.

## Oscillator Chip
#### Component
ABS05-32.768kHz-6-T
* [Mouser Link](https://www.mouser.com/ProductDetail/ABRACON/ABS05-32.768kHz-6-T?qs=XAiT9M5g4x8nsBWAGyPFJQ%3D%3D)

#### Relevant Specs
* 32.768 kHz Frequency
* 6 pF Load Capacitance
* -40 C Minimum Operating Temperature
* +85 C Maximum Operating Temperature
* Length 1.6 mm
* Width 1 mm
* Height 0.5 mm

#### Analysis
* 32.758 KHz
    * This was specified by the datasheet of the microcontroller.
* Capacitor values
    * The microcontroller datasheet strongly recommended the capacitor values follow the equation 2 * (oscillator load capacitance) - (capacitance of the microcontroller pins). The microcontroller pin capacitance was given at about 3 pF. The oscillator load capacitance was given at 12.5 pF. The final value of the capacitors were 22 pF. 
* Operating Temperature
    * The device can run with clean waveforms from –24 to 85 degrees Celsius. This should be perfectly acceptable for our operations. 

## SWD Connector
#### Component
485-4048
* [Mouser Link](https://www.mouser.com/ProductDetail/Adafruit/4048?qs=vLWxofP3U2w8elR0g2xP%252BA%3D%3D)

#### Relevant Specs
* 6.1 mm x 6.0 mm x 5.0 mm

#### Analysis
* Size Constraints
    * The size constraints for the SWD connector were the smallest possible.

## USB C Connector
#### Component
640-USB4085-GF-A
* [Mouser Link](https://www.mouser.com/ProductDetail/GCT/USB4085-GF-A?qs=KUoIvG%2F9Ilba1bQOahfWjw%3D%3D)

#### Relevant Specs
* Standard USB 2.0
* Type C
* Current Rating 3 A
* 8.94 mm x 9.17 mm

#### Analysis
* Size Constraints
    * The size constraints for the USB connector fit our size specifications

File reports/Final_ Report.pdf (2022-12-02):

# Final Report: Pipe Mapping via a Pass Through IMU Based System

Benjamin Ask
Department of Electrical and Computer Engineering Tennessee Technological University Cookeville, United States
baask42@tntech.edu

Caleb Thorne
Department of Electrical and Computer Engineering Tennessee Technological University Cookeville, United States
mcthorne42@tntech.edu

Adison Heathcott
Department of Electrical and Computer Engineering Tennessee Technological University Cookeville, United States
ayheathcot42@tntech.edu

Elizabeth Russell
Department of Electrical and Computer Engineering Tennessee Technological University Cookeville, United States
errussell42@tntech.edu

Abstract—This document is a model and instructions for LATEX. This and the IEEEtran.cls file define the components of your paper [title, text, heads, etc.]. *CRITICAL: Do Not Use Symbols, Special Characters, Footnotes, or Math in Paper Title or Abstract.
Index Terms—component, formatting, style, styling, insert
I. INTRODUCTION
1) Problem Statement: The main issue in pipe infrastructure is the money and time lost to locating the ‘lost’ pipes where the original surveys either were not recorded or were destroyed [9] [10]. The ‘lost’ pipes may malfunction due to a leak, need to be connected to a new system or may be ruptured due to construction that had no pipe on record which could be disastrous if the pipe were to be filled with gas or water. Issues that may result in a ruptured pipe can be as small as a leak to accidentally creating a spark and igniting gas in a pipe [8].
2) Document Summary: This project’s goal is to create a probe that can be guided through a length of pipe (20 to 40 feet of pipe) and collect data. This data will then be uploaded to a computer, which will receive, visualize, and plot the collected data to create a map of the pipe system. The subsystems of the resulting design are Power, Storage, Data Analysis, and Data Collection. These systems are atomized in Figure 1, but a short description of said subsystems is as follows: Power – contains the system concerning the supply of power to the system Storage – contains the system concerning the storage of data gathered by the probe Data Analysis – contains the system concerning the calculation on an external device of the data collected Data Collection – contains the system concerning the collection of data from the probe Movement - contains the system concerning the traversal of the probe through the pipe.
3) Expectations: A few specifications and standards for the pipe network that the team will test in are 1”-4” diameter pipes, 90 degree turns only, such as ‘elbow joints’ no ‘Tjoints’, and empty pipes with no water or gas contained within. Other concerns that may happen are things such as possible damage or error with the collecting of data which the team is planning to solve by having a redundant system to average with the main collection system to solve any error with the data collection. The ideal functioning of this probe and accompanying code will result in a probe that can map pipes in residential areas and will greatly reduce the cost of locating and uncovering said pipes.
A. Salient Outcomes
Our main successes came in the form of the mechanical testing system and the preliminary maps created during testing. We were able to create a fully functional testing system including a motor pulley system, probe casing compatible with said system and PVC pipe network.
B. Report Layout
Our report is organized as stated next: First a review of all the relevant literature, then our teams methodology, then our results and analysis, then a timeline and cost analysis of our project, then the ethical and professional considerations, followed by lessons learned throughout the process and the conclusion, with individual statements at the end of the paper.

II. LITERATURE REVIEW

A. Engineering Standards
The design of this project will adhere to all applicable standards, in both the professional and legal domains. The general PCB design, as well as the selection of its mounted components and peripherals, will adhere to the relevant IPC standards, which are listed below.
- IPC-2221B: Generic Standard on Printed Board Design
- IPC-A-600: Acceptability of Printed Boards

- IPC-A-610: Acceptability of Electronic Assemblies

The IPC standards will constrain this project in multiple ways, as these standards provide guidelines for virtually all aspects of PCB design [11]. Considering that the IPC standards will constrain the general layout of the PCB, such as trace widths, component distancing, and surface geometry, there will be a resulting constraint placed on which components must be selected in order to meet these overall standards. There will also be direct constraints placed on the components, as each component must be selected so that its rated values, such as power ratings, are not exceeded during any stage of the device’s operation. The Environmental Protection Agency (EPA) imposes constraints on certain types of batteries via the Mercury-Containing and Rechargeable Battery Management Act. Given that many common coin-cell batteries contain mercury [12], and thus fall within the scope of this law, it is a possible constraint for this project. In the event that this project implements a coin-cell battery anywhere on the PCB, the PCB layout may need to be designed in such a way that the coin-cell battery is easily removable from the device in order to keep it in accordance with the law.

III. METHODOLOGY

A. Data Collection Subsystem
1) Microcontroller: The microcontroller is the center of the probe and will be doing the most in terms of computation and power usage for the system. The team believes a low power STM microcontroller and custom board will be the most cost and performance efficient option. The team also has more experience in programming STM microcontrollers specifically, so the development of software should be easier.
Due to the constraints from the peripheral hardware and software the team needs to lay specifications on the microcontroller subsystem. This will assist in finding an adequate microcontroller that will support the needed hardware. Firstly, the microcontroller must be a 32 bit device to adequately support the 12 to 16 bit data it will be receiving from the peripheral IMU’s. It will also need to support memory addressing for the storage subsystem, which may be larger than 16 bits can support easily. Next, the microcontroller must have an adequate number of GPIO pins to support the peripherals and storage hardware. As of now the estimated number of minimum GPIO pins necessary are 50. This will allow extra pins to exist in case of need later and will be supported by a wide variety of microcontrollers. Finally, the microcontroller must allow an external clock source to be input for more accurate clock signals, and must support I2C, SPI, or USART for peripheral communications.
Each of the systems in the data collection subsystem will connect to the microcontroller using the pins of the microcontroller. Most systems will connect through either power or GPIO, however, some systems will connect to special pins on the chip, such as reset. The connections and their relationships will be discussed under each subsystem.
2) Clock: The clock subsystem is important since most microcontrollers do not have stable internal clocks. Most internal clocks are made of resistors and capacitors which can cause the clock signals to be inaccurate and noisy. [6] Timing is very important for calculating positions, communicating with peripherals, and ensuring the correct amount of power is used. Peripherals such as I2C and SWD need accurate clock signals to function correctly. The clock is also one of the most power consuming parts of a microcontroller and needs to be exact to ensure battery life calculations are accurate. The teams solution is to connect an external crystal oscillator to the microcontrollers pins to supply a more precise clock signal to the device.
3) Programming: The programming subsystem will allow the team to upload new software to the device much easier during development and testing. Most microcontrollers do not support software uploading systems out of the box, so a system needs to be developed to allow the user to upload new software from a USB connection.
JTAG and SWD are the main standards for communication when it comes to software uploading. SWD uses two GPIO pins, only supports ARM architecture, and supports printing debug information. JTAG uses four GPIO pins and supports multiple architectures including ARM. [7]
The team has decided JTAG will be the most beneficial due to its wide support for architectures. The system will need to have connections to the microcontroller GPIO pins and the USB port.
4) External Communication: The external communication subsystem will take care of power and data from the USB attached to the probe. The circuitry will determine what pins from the USB are sent to the power subsystem, and what data pins are sent to the correct subsystem for retrieval or reprogramming. The physical representation of this on the board will be a USB socket and simple wiring for splitting the input pins.
5) Reset: The device will always be under the threat of software or hardware bugs that could lock up the system. To counter this a reset system will be implemented onto the device. This will give the user a button or switch to interact that will be connected to the reset port on the microcontroller. Hard reset will always be accomplished by turning the probe off and resetting the power. This subsystem will supply the user a fast and efficient way to reset the software and peripherals without interrupting power supply.
6) State: The system will have multiple different states it can be in for operation. These states need to be defined in ways where the user can see the current state, and set new states.
For this a switch will be used to set the microcontroller and peripheral hardware into whatever state it needs. This will include a state for collecting data, retrieving data, writing new code, and enabling / disabling the device. This system will be connected to the microcontroller through GPIO pins that will tell the software what state to run in.

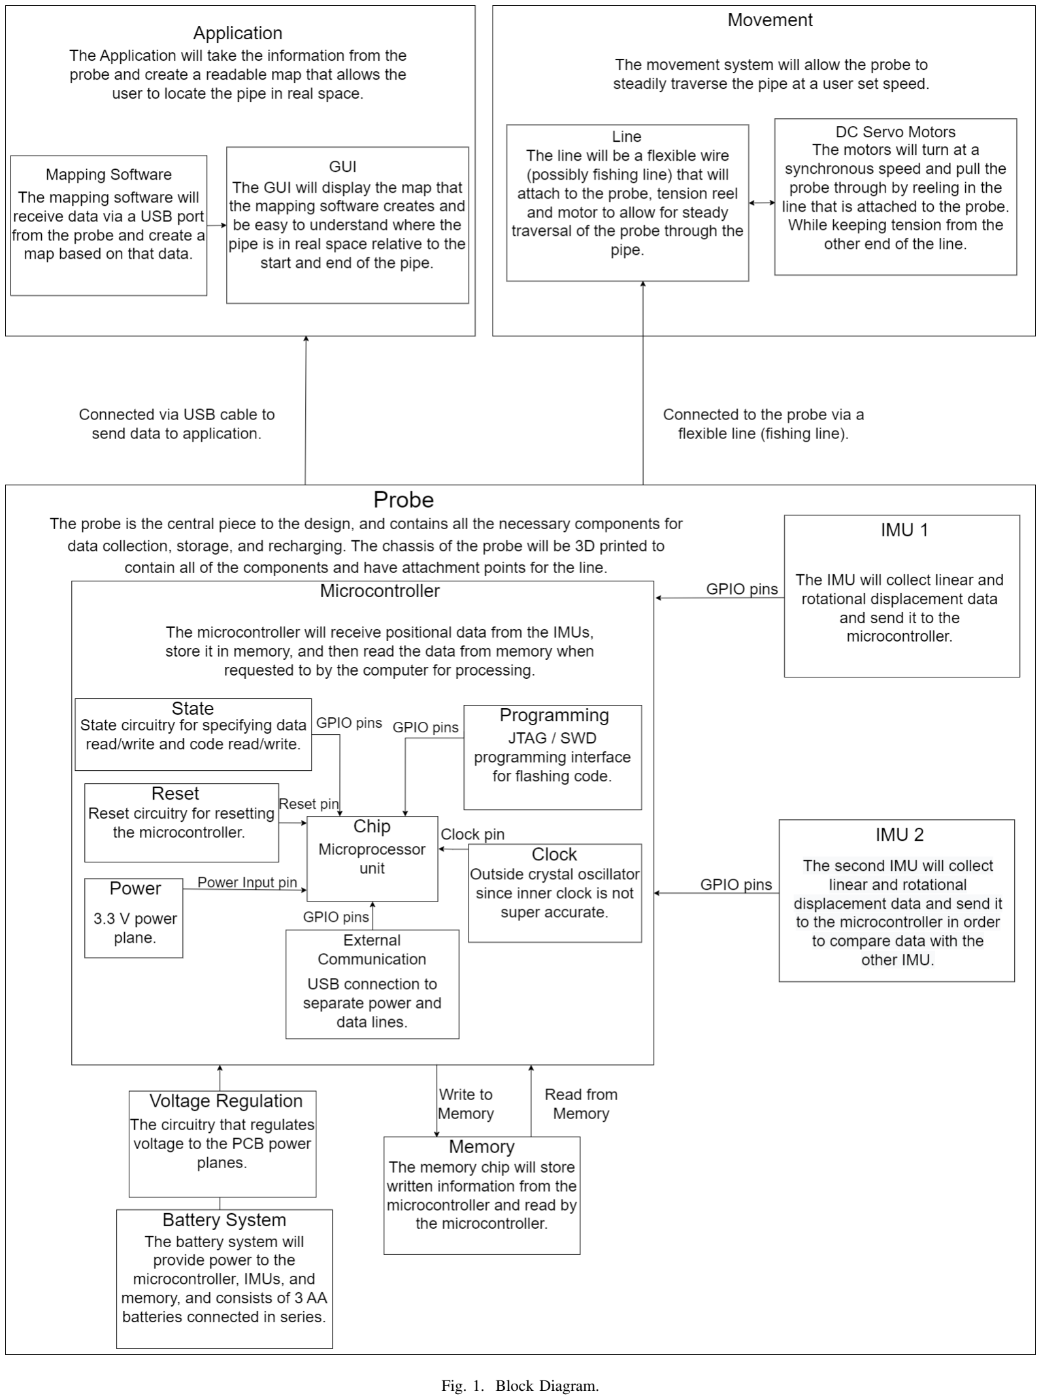
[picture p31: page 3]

Fig. 1. Block Diagram.

7) Acceleration Measurements: Measuring the acceleration of the device as it traverses the pipe is an integral part of the mapping process. Rather than using discrete accelerometers and gyroscopes, this project will utilize inertial measurement units (IMUs) in order to collect the position data. One component of an IMU is its 3-axis accelerometer, which will be used to measure the device’s acceleration through the pipe. The accelerometer has very few constraints since it creates more than it needs to adhere to. Firstly, most accelerometers have more than adequate sensitivity for the project. Secondly, most accelerometers support I2C, SPI, USART, and temporary data storage which will be supported by almost any microcontroller. Most accelerometers also run at a high enough frequency to have more than enough data points and to minimize the error gathered through the process.
8) Rotation Measurements: Keeping track of the device’s rotation is crucial for the task of mapping, as the rotational data will quantify any directional changes that the device makes. This measurement of the device’s rotation, which will be taken by the IMUs 3-axis gyroscope, will be used alongside the acceleration data in order to obtain an accurate representation of the area traveled by the device.
While the gyroscope is a separate component it adheres to the same constraints and specifications as the accelerometer since they will be coupled into the same device.
9) Error Measurements: There are a number of errors that can occur when using IMUs [2], though there are existing methods to help mitigate these errors. While most error reduction in this context will be accomplished by proper filtering, using multiple IMUs in tandem has been proven effective [3] in reducing the amount of IMU bias errors with respect to time. With this in mind, the team does intend to implement two IMUs in the design as a form of error prevention.
In regards to combating erroneous measurements via proper filtering, there are a few options that may be useful for this project. Utilizing a Kalman filter will likely be the best option however, as this method is specifically useful for predicting a device’s location over time. [4]. Kalman filtering is also well documented as a filtering method for IMUs in particular [5], which makes it a promising method of error correction for this device. This filtering will be done via computer software once the device is connected.
B. Storage Subsystem
1) Memory Chip: The memory chip subsystem will handle the storage and retrieval of the data sensed by the probe. It will need to be able to hold at least 5000 feet of data and keep the data over a reset or power off signal. The memory chip will be connected to the microcontroller through GPIO pins and will be connected to the power subsystem through the power and ground lines.
The memory needs are difficult to predict, however, they can be roughly estimated. The worst case accelerometer data collection will be 1000 Hz with 16 bits of data. The longest pipe the team expects to support is 5000 feet. An estimated 20 minutes will be needed to traverse the pipe. At 20 minutes the device will collect around 10 MB of data. This will be the teams estimated constraints on the memory size for the storage subsystem.
C. Power Subsystem
1) Battery: As this device will be designed to operate without a constant supply of wired power, a rechargeable battery (or series of batteries) will be necessary in order to keep it powered as it traverses the pipe. The battery subsystem will have connections with the voltage regulation, voltage measurement, current measurement, heat measurement, and microcontroller subsystems.
To properly support the hardware the team is planning on getting a battery that at least supports a maximum 3.6 V - 5 V voltage with 1Ah. With the lower amperage needs of all the devices 1Ah should suffice and will be decently easy to acquire.
2) Voltage Regulation: The voltage regulation subsystem is responsible for regulating the battery voltage to the device while it is powered on, supplying the appropriate voltage to each of the other connected subsystems. This voltage regulation will be accomplished via a 3.3V LDO for powering the microcontroller, and a 1.8V LDO for powering the IMUs and memory. This subsystem will be connected to the battery subsystem, and the PCB power planes
D. Data Analysis Subsystem

To minimize the work and complexity of the microprocessor, the job of calculating mapping and visual data has been moved to an external program. The program will acquire data from the device using a USB and will use various programs to convert the acceleration and rotation data into 3D position data. It will also calculate and minimize error with software filters.
1) Mapping: The mapping application will be implemented on MATLAB due to its helpful libraries and strong computational power. The program will first acquire the acceleration and rotation data, convert them into 3D positional data, and filter out any noise or drift caused by integration. Then the points can be converted and charted to show distance, lengths, and other important information for location.
2) Filtering: A large part of the application will be filtering out extra noise produced by the variability of the gyroscopes and accelerometers. For this, the team will use software Kalman filters in either Matlab or Simulink.
3) Visualizing: The visualization application will be implemented on both MATLAB and any 3D model program possible, such as 3D viewer on Microsoft Windows. The program will first take the 3D data and convert this data into vertices that can be rendered to visibly show the pipe layout. These vertices will give users the ability to view to 3D pipe network using any program that will render obj files.

IV. CONSTRAINTS, SPECIFICATIONS, AND ANALYTICAL VERIFICATION

A. Power
The power subsystem must be capable of supplying 3.6V to 5V to the device, as this should be sufficient for powering the microcontroller as well as its attached peripherals. In addition, the battery must be able to store at least 1 Ah of charge, which should be sufficient for the low-power needs of an STM microcontroller and the sensors. Many STM microcontrollers and IMUs come equipped with various options for powersaving modes, which will also help to conserve battery usage on these already low-power devices. This battery must also be rechargeable, which will place a constraint on what type of batteries can be used for this project. Finally, as the device will begin recharging when plugged into a computer, the power subsystem will need to be capable of receiving input power via USB ports of a computer. Depending on what version the USB ports are (2.0 or 3.0), the input voltage to the power subsystem will differ, which means that the power subsystem will need to be capable of accepting a range of possible input voltages.
In order to verify that the specifications of the power subsystem are met, analysis may be performed via simulation software, such as LTSpice or Multisim, as well as via manual calculation using principles of circuit design.
B. Storage
The storage subsystem shares a mutual constraint with the microcontroller, as the memory chip will need to exchange information with the microcontroller at the appropriate times in the clock cycle. In order to meet the specifications defined in Section II.B of this document, the memory chip will be capable of storing 100 MB at minimum. In order for the memory chip to retain the data when the device is powered off or reset, as also specified in Section II.B, this subsystem will need to be designed with a nonvolatile variety of memory. The team believes that using a flash memory chip will be a suitable option to meet this design specification. This subsystem, like most of the other subsystems, will also be constrained by the physical size restriction placed on the device as a whole (being small enough to traverse a 1” to 4” diameter pipe). The memory chip chosen must be as small as possible, while still meeting all of the above specifications.
The memory subsystem may be analytically tested via hand calculations. The team will verify that the memory chip will be suitable with calculations based on the microprocessor clock speed, read and write times of the chip in question, power requirements of the chip, and any other relevant information that needs to be considered.
C. Microcontroller
The microcontroller will need to be a 32 bit system, since the IMU output data is typically either 12 or 16 bits. In order to have enough pins for interfacing with all of the peripherals, the microcontroller must also possess a minimum of 14 GPIO pins, as well as the ability to support JTAG and I2C communication protocols. The microcontroller must also be capable of connection to an external clock generator, as the microcontroller design will implement an external crystal oscillator to aid in maintaining clock precision. The microprocessor in particular will also have constraints placed on it by the IMUs and memory chip, as the clock frequency of the processor must be high enough to support all of these peripherals while maintaining a suitable sampling rate for these devices. The microcontroller must also fit within the maximum footprint of the device, which will need to be small enough to traverse a pipe as small as 1” in diameter.
The microcontroller design will be analytically tested via a suitable emulator with STM32 support, such as Qemu.
D. IMUs
In order to ensure the highest data resolution possible from both of the IMUs, the team will select a device that provides 16 bit output resolution from both the accelerometer and gyroscope components. The IMUs must also draw a low amount of power, on the scale of milliamps, in order to ensure that the power subsystem is capable of supplying enough power to all device subsystems. The IMUs will also be constrained by the size specifications mentioned in the previous sections.
The IMUs will be analytically tested via Matlab and/or Simulink, as there are a variety of existing methods for IMU simulation on those platforms.
V. RESULTS
A. Experiment 1
The first experimentation we did was on the mechanical subsystem which includes the motors, pipe network, and spool with fish line. The completed experiment consisted of a ”dummy” battery holder shell being pulled through the 24 foot long 2 inch diameter PVC network. While the probe was being pulled through we kept a running graph of the instantaneous motor velocity and found the largest difference between the desired velocity and the actual velocity of the motor (data shown below). Screenshots of the graphs have been provided below to show how the data was collected.
Motor Velocity Deviation Table
Run Number | Set Velocity (ft/sec) | Max Velocity Deviation (ft/sec)
1 | 1.39 | 0.016
2 | 1.36 | 0.060
3 | 1.34 | 0.038
4 | 1.41 | 0.019
5 | 1.27 | 0.052
B. Analysis & recommended Improvements
One problem that we encountered with this system is that while the battery shell easily traversed the network, the PCB shell often got stuck in the 2” 90 degree elbows due to a small lip that was not forseen in our initial design. Our next step is to redesign the PCB shell to have a more gradual edge rather than being very nearly a perfect cylinder. It is likely that both the battery shell and PCB shell would fit in a larger diameter PVC system but our cost for testing would have had to be much higher to confirm that theory. What this experiment verified was that our mechanical subsystem pulls at or above our minimum velocity (1 ft/sec) and pulls consistently with very little deviation so as to minimize the error during data collection. While we did not have a specific number constraining our velocity deviation we found that the deviation was always less than 0.1 ft/sec in each of our five tests which means if we run our probe around 1 ft/sec then we will never exceed our maximum velocity of 2 ft/sec which was calculated based on our sampling rate. Therefore this system successfully remained within the constraints while meeting specifications.
C. Experiment 2
The second experiment was designed to test the accuracy of the probe and to see if the data measured produced data within our specifications. Our constraints define a successful plot to be within a 1” radius of the measured pipes edge. For the following iterations of the experiment, it was not possible to measure the probes location from inside a 2” pipe. Instead, the probe was run over four separate paths defined by duct tape on the floor and walls. For each of the experiments it is assumed that the start location of the probe is (0, 0, 0) on a 3D axis defined as (x, y, z) and the probe is facing the positive y direction.
1) Experiment Iteration 1: For the first iteration the tape line is plotted as the orange line on the graphs, however, a text description is included here as well. The first run consisted of a straight line exactly 6.14 meters long. The second run consisted of a straight line for 3.35 meters, a right turn, and another straight line for 3 meters. The third run consisted of a straight line for 2 meters, a turn upward, and a straight line for 4.14 meters. The fourth run consisted of a straight line exactly 2 meters in length.
The graph below shows the network number and run number for each experiment, the sample rate the data was captured at, the threshold value set in the software, and the final point of the measured data minus the final point of the baseline. The threshold value is set in the software and defines the minimum normalized acceleration that would constitute the probe as ”moving”. The difference of the final points is represented as (x, y, z) with each value being the distance between the two points on their respective axis.
Pipe Mapping Results
It is difficult to represent the deviation through the path without having tables full of thousands of data points, so the graphs below show the baseline (orange) and the measured line (blue). The endpoints have been measured to give some metric of how far off the final values are, but the intermediate values need to be evaluated graphically. Note in some of the graphed simulations the orange line is difficult to see but it is there.
2) Experiment Iteration 2: For the second iteration the same data from iteration 1 was used. The first iteration shows
Network - Run Number | Threshold | Endpoint Error (meters)
1 - 1 | 0.1 | (7.05, 6.16, 2.32)
1 - 2 | 0.1 | (4.98, 7.22, 1.02)
1 - 3 | 0.1 | (5.54, 1.18, 2.22)
2 - 1 | 0.1 | (0.41, 0.50, 2.72)
2 - 2 | 0.1 | (13.0, 21.4, 8.72)
2 - 3 | 0.1 | (13.3, 4.71, 4.76)
3 - 1 | 0.1 | (97.1, 5.70, 50.3)
3 - 2 | 0.1 | (10.7, 0.67, 2.18)
3 - 3 | 0.1 | (27.4, 4.14, 29.8)
4 - 1 | 0.1 | (87.9, 199.4, 612.3)
4 - 2 | 0.1 | (24.4, 73.1, 214.1)
4 - 3 | 0.1 | (18.3, 108.4, 183.8)

a large amount of variability in the final measurements from endpoints and does not always follow the baseline path shown in the graphs. Our first assumption is to test the gyroscope to see if this is the basis of our errors.
Below are graphs and table entries of Pipe 1 and Pipe 2 with the gyroscope data set to 0.
Network - Run Number | Threshold | Endpoint Error (meters)
1 - 1 | 0.1 | (5.80, 2.44, 2.30)
1 - 2 | 0.1 | (5.92, 1.38, 1.16)
1 - 3 | 0.1 | (5.96, 3.09, 2.26)
2 - 1 | 0.1 | (4.28, 2.24, 2.64)
2 - 2 | 0.1 | (6.15, 1.07, 1.70)
2 - 3 | 0.1 | (2.76, 4.54, 4.93)

Even though our endpoints are closer, the data does not follow the path of the baseline. This led the team to believe that the gyroscope should not be the issue. However, we are not ruling out the possibility.
3) Experiment Iteration 3: For the third iteration the team wanted to test whether the speed and acceleration had anything to do with our skewed results. For this a new set of data was generated with new experimentation. The probe was moved along new and old paths similarly to the methods before, except the speed was increased. Initially, the speed was around 0.8 feet per second. The new speed is around 2.5 - 3 feet per second. These values are estimated from the time and distance covered by the retrieved data, we do not have the means to travel at an exact speed since our system can not be integrated with the mechanical system.
The first pipe was moved along a straight line 9.144 meters in length. The second pipe was moved along the path of pipe 2 in the initial experiments, 3.35 meters straight and 3 meters to the right. For this iteration the gain value was adjusted to get better results. The gain value controls the strength of the gyroscope based error correction on the system.
Network - Run Number | Threshold | Endpoint Error (meters)
1 - 1 | 0.21 | (0.63, 1.60, 1.76)
1 - 2 | 0.21 | (2.63, 1.94, 1.08)
1 - 3 | 0.21 | (2.70, 2.00, 1.10)
2 - 1 | 0.12 | (0.94, 5.38, 2.65)
2 - 2 | 0.2 | (1.73, 1.86, 1.73)
2 - 3 | 0.2 | (3.01, 1.05, 0.217)

These results look closer to the baseline, however, they are not perfect. This increase in speed has shown to give better data, most likely due to more pronounced data in the IMU.

Most experiments using this new iteration turned out similarly to those shown above. The team believes that if the speed was more consistent throughout the experiment the data would be even closer to the baseline.
4) Experiment Iteration 4: In the third iteration we increased the speed to obtain better results. Increasing the speed means a faster experiment time, which in turn means less data points in the experiment. Due to this we decided to increase the sampling rate to see if the data would be more defined. If you increase the sampling rate, you increase the amount of data obtained in the same amount of time. This data then has to be written to the memory for storage. This in turn poses a trade-off which we had to consider. The faster the sampling rate, the longer the memory would take to write, and the more gaps we would have in the data. The slower the sampling rate, the shorter the memory would take to write, and the more continuous the data would look. Due to this we settled on doubling the sampling rate from 26 Hz to 52 Hz.
Network - Run Number | Threshold | Endpoint Error (meters)
1 - 1 | 0.55 | (3.75, 2.92, 0.95)
1 - 2 | 0.35 | (1.00, 2.04, 0.75)
1 - 3 | 0.45 | (2.70, 2.00, 1.10)

These results show that the increased sampling rate helped with more accurate turns. However, it still wasn’t fast enough to show any increased accuracy in the measurements. As stated above, changing the sampling rate provides a trade-off. The team feels as if 52 Hz was the last possible rating for the IMU that would give decently accurate data without adding large holes in the sampling.
5) Experiment Iteration 5: The fifth experiment was used to test if the ’free fall’ of the IMU would cause errors in the measurements. For this we held the probe 3 feet in the air and dropped it suddenly. Measurements were taken for a short time before and after the fall to measure the baseline of no movement.
Network - Run Number | Threshold | Endpoint Error (meters)
1 - 1 | 0.1 | (0.022, 0.55, 0.46)
1 - 2 | 0.25 | (0.009, 0.045, 0.088)

This experiment showed that even though the drop was not always consistent and correct, it shouldn’t be causing any large error in our calculations. The errors seen were predicated as the IMU was not expected to always give accurate results in free fall. We had hoped to have more runs and larger heights, however, concern over damaging the probe caused us to end experimentation fairly quickly.
We performed this experiment to test if our previous assumptions of free fall were true and to test the scale of impact. Previous experiments had no reason to be affected by free fall since none of the were dropped uncontrolled. We are now confident that the current system we have employed will handle downward motion adequately and that the chance of free fall will not cause any large errors.
6) Experiment Iteration 6: The sixth experiment was used to test the baseline of no movement. This could be used to see if the IMU had any internal errors or if the software was interpreting still movement incorrectly.
Network - Run Number | Threshold | Endpoint Error (meters)
1 - 1 | 0.3 | (0.0015, 0.002, 0.0005)
1 - 2 | 0.3 | (0.0015, 0.002, 0.0001)

The experiment results show that the still movement gives accurate results and that the error is extremely minimal. It is difficult to see the baseline in the graphs but they are present at (0, 0, 0).
7) Experiment Iteration 7: The seventh experiment was used to test if the constant speed of the motors would give better results. The experiment itself had some minor problems that were unavoidable. Firstly, the path was only able to be set up in a short straight line. We were only able to mount the motors to the table so the track could only be the length of the table, 2 meters.
Secondly, the probe had to be put on a box that was then pulled to keep the probe, and the wires safe. The extra friction and caused the probe to move differently than it would have through the pipe in the casing. Also the motor spools needed room to be able to spin so the edge of the table was utilized. This also caused the box to need extra stabilization which caused some tilts in the readings.
The experiment was engineered to be the best it could given the circumstances, but it is not perfect.
Network - Run Number | Threshold | Endpoint Error (meters)
1 - 1 | 0.4 | (2.71, 1.45, 1.42)
1 - 2 | 0.4 | (1.99, 0.99, 0.22)

The results were not what the team was expecting but they still seem promising. Due to the experimentation problems the results were predicted to come out with some error. This level of error was not predicted but is explainable.
Again, the team feels that if the correct hardware and experimentation parameters were met, the results would be much more accurate.
8) Analysis and Recommended Improvements: Our initial experimentation showed large amounts of variability in the final measurements from the endpoints and didn’t always follow the baseline path. Error was to be expected initially, but not to this degree. We conducted further experiments to isolate the cause of the error. In these further experiments, the gyroscope was ruled out as a culprit and the speed was brought to light. The later experiments still show error in the recordings but we think we have plausible evidence on what is causing the error.
Firstly, the state of the current drone is causing some of the error, or inability to prevent error, that is difficult to mitigate without redesign. The size and fragility of the current probe keeps it from being tested in its originally designed fashion. The probe cannot fit in the pipe since the wires and extra hardware takes up much more space than would fit inside the pipe. The fragility of the wires also prevents us from testing the system with the mechanical subsystem, as the wires are too delicate to risk such an experiment.
Our second source of error is very similar. Due to the fact that we cannot use the mechanical subsystem in the current design, we cannot move the drone at a consistent speed. Experiment iteration 3 shows that increasing the speed gave better results and the team believes a more constant speed would also help after further investigation into the software. We have also come to the conclusion that we need to increase the speed of the probe. This is possible, however, we have selected the current speed to be the least damaging to the probe and the pipe. The redesign would need to ensure that the pipe could endure faster speed than previously calculated and that the new casing would be designed to safely travel at those higher speeds.
The last cause of error, is due to the software using dead reckoning to map the data points. Dead reckoning is at its base an estimation to be able to map a path using the data points, this error will always exist in our program. Dead reckoning uses the position measured and velocity to plot your position. Dead reckoning (originally called deduced reckoning) will always introduce slight error into the system, one reason is due to the fact that to get the velocity needed for the position calculation, you must integrate the acceleration which adds an unknown C constant. Then to get a position from that velocity it must be integrated again which changes the equation to end in Cx+D where C and D are unknowns. This C and D introduce error, as the number of integrations increases over time to gain the needed positions the error will grow.
There are two ways to mitigate this error, one is to zero out the error every so often when the software is run and the second is to have a secondary unit such as a GPS, LIDAR, or external sensor to gain the true location so that the error can be calculated out.
Unfortunately, as we are only using data from 6-axis IMUs dead reckoning is the only calculation that was feasible, as our group is only using an accelerometer and gyroscope to gather data. Another fix would be to get a higher quality IMU where it has a secondary unit included. Our code does have error mitigation already added, so to properly lowered the error to near zero we would need to utilize a secondary sensor.
Our solution was originally planned to mitigate some of these errors. However, as we faced many difficulties during implementation, we had to forego components and methods that were going to assist in reducing this error. Due to this we do not meet our 1” goal for the error range, however, we do have ideas on ways to mitigate this error and design a better system.
Firstly, having the second IMU to check measurements and give better filtering data would be extremely helpful and is already implemented in the redesign. Secondly, having the probe fit inside the casing, and thus the pipe, would hopefully give the sensors a more stable and constant environment to record data in. We could mitigate a lot of sudden movements, accidental offsets, and we could keep the speed much more constant. Finally, having secondary systems, like a GPS or magnetometer, would help tremendously since IMUs have difficulty measuring the incline/decline in a path and are sensitive to sudden changes in motion.
Even though the team was not able to get the data within the margins of success, we believe we have determined the cause of the error and have hypothesised on possible fixes to this error. We have taken individual tests of all the subsystems, software, and hardware pieces. The memory is tested in Experiment 3 and shows perfect execution. The software has been tested with example data and shows to be a promising asset. Finally, the IMU is tested in this experiment, however, it is difficult to break down the system any further than we already have.
We believe that the best way to fix the error in our system would be to move forward with the redesign and conduct the original experiments in the way they were first imagined, with one small change. We would like to run the experiments with varying speeds to truly test what constant speed would give the best results before the sampling rate would need to be increased.
D. Experiment 3
The third experiment was designed to test the capabilities of the memory subsystem. We used this experiment to validate that the memory would be able to hold up to 5000 feet or 20 minutes worth of data, and to keep the data when the device was powered off and on. The experiment consisted of running the device for various time lengths, measuring the amount of data that was stored in the memory, verifying that the memory had not overflowed, and verifying that the data was still intact and unmodified.
We were able to use the timestamp provided by the IMU to measure the exact amount of time data was measured. The IMU was running at 26 Hz and polled both the accelerometer, gyroscope, and timestamp. Each data entry consisted of 7 bytes, 1 tag byte and 6 data bytes. Since the data rate and size were constant the data looks exactly as predicted.
Run Time | Bytes Stored | Bytes Retrieved | Bytes Remaining
1 minute | 32,760 | 32,760 | 16,744,456
5 minutes | 163,800 | 163,800 | 16,613,416
10 minutes | 327,600 | 327,600 | 16,449,616
15 minutes | 491,400 | 491,400 | 16,285,816
20 minutes | 655,200 | 655,200 | 16,122,016
1) Analysis and Recommended Improvements: The memory subsystem was easily able to collect data continuously for 20 minutes which is well above what it should ever actually have to collect in a real application. Recommended improvements are purely to increase the performance of the system and convenience of the programmer. The only improvement that the team could find was to change the memory to be able to be written to without being erased. The current memory has to be erased every time you want to change the data in a byte so this caused a bit of a performance hit on the system. It was not enough to change the data but if we sampled at a higher frequency, it would have caused a problem.

E. Experiment 4
The fourth experiment focused on verifying that the device’s battery life was within the specification defined within previous documents. This specification stated that the batteries must last long enough for the probe to collect 20 minutes worth of data at minimum. For this experiment, the device was powered only via the series connection of 3 AA batteries connected to the Vin and GND pins of the Arduino Nano. Load current was measured using a DMM, and then the initial battery voltage was measured. After recording the initial battery voltage, the device was allowed to continuously poll data for 20 minutes uninterrupted. After the 20 minutes were up, the battery voltage was measured again. This test was performed 3 times. The data is shown in the table below.
Test | Run Time | Initial Voltage | Post-Test Voltage | Load Current
1 | 20 minutes | 5.08 V | 5.03 V | 15-18 mA
2 | 20 minutes | 5.03 V | 4.98 V | 15-18 mA
3 | 20 minutes | 4.98 V | 4.92 V | 15-18 mA

Given the initial specification of 20 minutes minimum run time, this experiment verifies that the device comfortably meets our requirements. It should be noted that due to the dropout voltage of the 3.3V LDO, the device will only remain powered until the total battery voltage reaches around 3.67V. However, even though the device will only be functional until the battery voltage approaches this threshold, it is clear that the device exceeds our minimum run time requirement. Given the load current in the table above, and the manufacturer discharge curve for the batteries used in this experiment (Duracell Coppertop AA’s), we can estimate the battery life of the device to be around 50-100 hours when using these batteries.

VI. TIMELINE AND COST

VII. ETHICAL AND PROFESSIONAL RESPONSIBILITIES

A. Ethical Considerations
There are some considerations to be made regarding ethical design choices in this project, and the team has attempted to address all of them throughout the design process thus far. The primary ethical considerations for this project include the following.
1) Device Construction: The outermost surface of the device must be constructed in such a manner that it will neither damage, nor introduce potentially unwanted contaminants into the pipe network, whether during normal operation or in a failure case. This means that special care will need to be taken in regards to choosing the material making up the outermost surfaces, as well as properly protecting any potentially harmful chemicals contained within the device, such as battery acid.
2) Device Lost/Stuck in Pipe: The possibility that the device could become, lost, stuck, or otherwise irretrievable from the pipe network is also an ethical consideration, as this event could potentially result in negative consequences affecting humans, structures, and/or the environment in certain failure cases. If the device gets stuck in an empty water pipe, and water begins to flow into the pipe before the device is removed, the blockage caused by the device could lead to pressure buildup that is excessive enough to cause the pipe to rupture. In this case, there could be direct harm caused to any individuals within close proximity to the ruptured pipe, as well as the surrounding structure. This break in the line would also prevent water from flowing to its intended destination, which could result in an outcome ranging anywhere from inconvenient to catastrophic, depending on what the water source was supplying. Depending on the chemical contents of the leaking water, (i.e., wastewater or drinking water), the burst pipe could also present an environmental hazard. In the case that the pipe carried gas rather than water, the pressure buildup resulting from a blockage caused by the device could result in a rupture of the pipe, which could then result in ignition of gas present in the line, depending on the properties of the gas.
With this being said, it is critical that the device be designed and constructed in such a manner that the probability of the device becoming stuck inside the pipe is minimized. The device will be designed with a minimal footprint, also taking into account the reduction in space that will occur in the bends of the pipe, such as 90 degree elbows.

VIII. LESSONS LEARNED

* We ran into a time crunch due to shipping delays. In the future we would definitely prioritize early ordering of parts. * During assembly we had a key part (our microcontroller) burn out. This caused us to have to completely reconfigure our design. In the future we would either negotiate to order double what is needed, or plan a backup part if the chip/part is defective. * When at all possible, avoid using leadless IC’s when designing a surface-mount PCB. Without the right equipment, it is incredibly challenging to solder correctly. * We found that our leadless SMD components were extremely difficult to solder. In the future we would make sure to get a stencil for reflow soldering the board. * We found that our error was much larger in the mapping than expected and it turned out that we likely need another component e.g Lidar, magnetometer or GPS to decrease this error. In the future we would add more systems to increase mapping accuracy and in general be wary of the accuracy of a single IMU with little filtering. The team determined that using a set of 9-axis IMUs rather than the 6-axis set we used would greatly assist in keeping the gyroscope measurements accurate.

IX. CONCLUSION

In conclusion we as a team have accomplished a great deal. We were able to create a working test setup for the mechanical side of things (Probe casing being run through the PVC). We were also able to build a fully operational hardware setup for testing. We were able to generate 3D maps from our testing. For future work we would most like to improve upon the PCB and the mapping accuracy. We have a fully ready PCB rework and have many ideas on how to increase the accuracy of our mapping software.

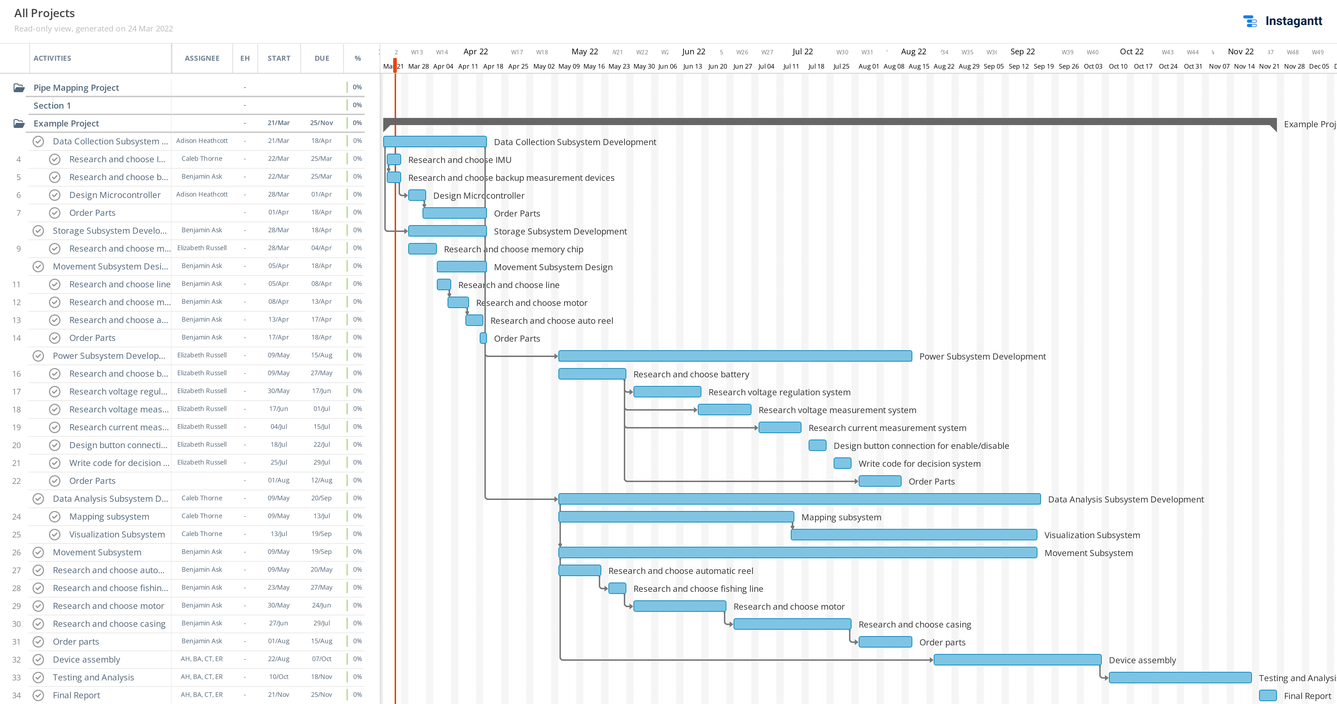
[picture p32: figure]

Fig. 2. Gantt Chart

INDIVIDUAL STATEMENTS
A. Adison Heathcott
In previous coursework I learned a lot of things that were very helpful in this project. Some are listed below:
- Circuit and Electronics Design and Analysis
- Microcontroller Design and Programming
- Signal Processing
- Physics
During the course I learned, and had to teach myself, a lot. Examples are listed below:
- PCB Design and Debugging
- Electronics Debugging
- Python and KiCAD
- Working long term with a team on time sensitive projects.
- Improved Presentation Skills
- Improved Project Planning Skills
B. Benjamin Ask
In previous coursework I learned...
- How to analyze a circuit
- How to integrate electronics
- Calculus based physics
- Professionalism (how to present work, how to work in a team)
- How to program using C++
- What a microcontroller is and how to implement it During the course of this project I learned...
- Gained a deeper understanding of motors, and motor controllers (for the mechanical subsystem)
- Gained a deeper understanding of the physics involved in pulling probe through PVC (for the mechanical subsystem)
- How to better operate within a team (during project planning and assembly)
- Better presenting skills for technical presentations (design phase 1 presentation and final presentation especially)
- How to create and use a Gantt Chart for timeline management (gave us an understanding of how long we had to work on each piece of the project)
- How to use a motor controller to achieve consistent velocity of a motor (for the mechanical subsystem testing)
- How to brainstorm solutions to a unique problem (encompasses the entire project proposal)
C. Caleb Thorne

Previous coursework equipped me with several skills that were helpful in this capstone project, such as:
- Analog circuit analysis
- Calculus based physics
- Signal processing fundamentals
- General soldering techniques
- Use of test equipment (Oscilloscopes, DMMs, etc.) Over the course of this project, I also learned:
- Techniques for soldering SMD components by hand
- How to use a reflow oven and stencils to solder leadless SMD packages
- Methods of troubleshooting PCB prototypes, and improvising creative solutions in the case of hardware failure

- General project management skills
- Improved presentation skills; particularly technical presentations
- How to successfully cooperate with a team that is designing both hardware and software in tandem
- How IMUs can be functionally implemented for mapping, and how much software/filtering work is required to achieve adequate results with them
D. Elizabeth Russell

Topics that I learned in prior courses which were helpful in this project are listed below.
- Circuit and electronics analysis
- Electromagnetic fields
- C++ and programming logic
- Calculus based physics
- Telecommunication and signal fundamentals During this course I learned:
- To utilize and read Python code
- Application of telecommunication techniques
- How to improve my public speaking and presentation skills
- The ways IMU data can be used in mapping
- Ways to troubleshoot code
- How IMU data can compound errors and ways to solve those errors
- To successfully communicate and cooperate with a team in relation to time sensitive projects
- What ways are best when finding facts on lesser known information
- Improved problem solving skills

REFERENCES

[1] G. Zeiss, “Inertial mapping of Underground Pipe Networks,”
Between | the | Poles, | 10-Dec-2019. | [Online]. | Available:
https://geospatial.blogs.com/geospatial/2019/12/inertial-mapping-ofunderground-pipe-networks-.html. [Accessed: 12-Feb-2022].
[2] W. | Heinselman, | “What | is | trenchless | pipe | replacement
and | how | much | does | it | cost?,” | What | is | Trenchless | Pipe
Replacement | and How | Much Does | it | Cost?, | 04-Aug-2017.
[Online]. | Available: | https://www.expresssewer.com/blog/what-
is-trenchless-pipe-replacement-and-how-much-does-itcost#: :text=Conventional%20dig%20and%20replace%20pipe,are%20 longer%20than%2050%20feet. [Accessed: 17-Feb-2022].
[3] “The | Tools | Necessary | For | Underground | Pipe | Installation,”
https://www.catrentalstore.com/en US/blog/underground-
pipe-installation.html. | [Online]. | Available:
https://www.catrentalstore.com/en US/blog/underground-pipe-installation.html. [Accessed: 17-Feb-2022].
[4] PVC Chemical Resistance Guide, 1st ed. Oakville, Ontario: Ipex, 2020, p.6 [Online]. Available: https://www.ipexna.com/media/11116/chemicalguide-en-ipex-pvc.pdf. [Accessed: 17- Feb- 2022]
[5] Charlotte | Pipe | and | Foundry | Company, | [Online]
https://www.charlottepipe.com/price lists.aspx. | [Accessed:17-Feb-
2022]
[6] Digikey | Electronics, | [Online] | Available:
https://www.digikey.com/en/products. [Accessed:17-Feb-2022]
[7] “History of plumbing in America,” PlumbingSupply.com. [Online]. Available: https://www.plumbingsupply.com/plumbing-projectsand-information/toilet-history-america. [Accessed: 23-Feb-2022].
[8] “Fact | sheet: | The | biden-harris | lead | pipe | and | paint | action
plan,” | The | White | House, | 16-Dec-2021. | [Online]. | Avail-
able: | https://www.whitehouse.gov/briefing-room/statements-
releases/2021/12/16/fact-sheet-the-biden-harris-lead-pipe-and-paintaction-plan/. [Accessed: 23-Feb-2022].
[9] “NFPA 70®,” NFPA 70®: National Electrical Code®, 25-Aug-2019.
[Online]. | Available: | https://www.nfpa.org/codes-and-standards/all-
codes-and-standards/list-of-codes-and-standards/detail?code=70. [Accessed: 23-Feb-2022].
[10] P. | Musungu, | “Utilizing | inertial | navigation | technology | for
3D Mapping, locating and managing underground pipelines,” Construction Review Online, 21-Aug-2021. [Online]. Available: https://constructionreviewonline.com/machinery-equipment/utilizinginertial-navigation-technology-for-3d-mapping-locating-and-managingunderground-pipelines/. [Accessed: 26-Feb-2022].
[11] “How to track underground water pipe?,” EngineerSupply, 04-Oct-2021. [Online]. Available: https://www.engineersupply.com/How-To-Track-Underground-Water-Pipe.aspx. [Accessed: 26-Feb-2022].
[12] ”NCHRP 15-44 GUIDELINES FOR THE USE OF MOBILE LIDAR IN TRANSPORTATION APPLICATIONS”, 01-Feb-2013. [Online]. Available: https://onlinepubs.trb.org/onlinepubs/nchrp/docs/nchrp15-44 finalguidelines.pdf
[13] “VR positional tracking,” Wikipedia, 18-Feb-2022. [Online]. Available: https://en.wikipedia.org/wiki/VR positional tracking. [Accessed: 27-Feb-2022].
[14] Sagar, | “Applying | IPC-2221 | standards | in | circuit | board
design,” | Sierra | Circuits, | 18-Jan-2022. | [Online]. | Available:
https://www.protoexpress.com/blog/ipc-2221-circuit-board-design/. [Accessed: 27-Feb-2022].
[15] “Mercury in Batteries,” EPA, 07-Jan-2021. [Online]. Available:
https://www.epa.gov/mercury/mercury-batteries. | [Accessed: | 27-Feb-
2022].
[16] “Low | power | radio | - | general | information,” | Federal | Com-
munications | Commission, | 01-Sep-2021. | [Online]. | Available:
https://www.fcc.gov/media/radio/low-power-radio-general-information. [Accessed: 27-Feb-2022].
[17] “Guide to Wireless Regulations in the United States,” 09-Feb-2015. [Online]. Available: https://www.linxtechnologies.com/wp/wpcontent/uploads/fcc resource document.pdf. [Accessed: 27-Feb-2022].
[18] “Simultaneous Localization and Mapping for Inspection Robots in Water and Sewer Pipe Networks : A Review,” sept-2021. [Online]. Available: https://www.researchgate.net/publication/354874891 Simultaneous Local ization and Mapping for Inspection Robots in Water and Sewer Pipe Networks A Review. [Accessed: 27-Feb-2thebibliography022].

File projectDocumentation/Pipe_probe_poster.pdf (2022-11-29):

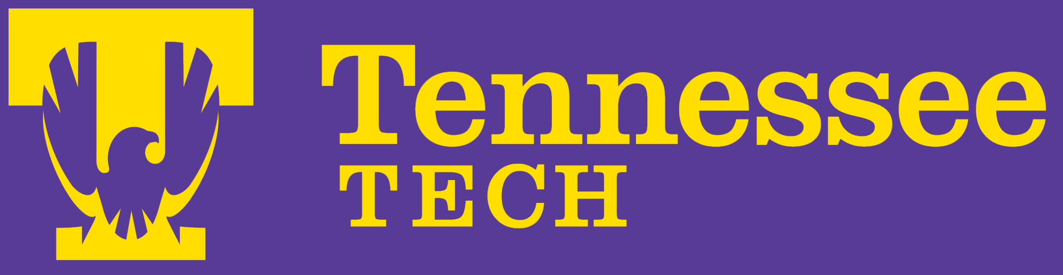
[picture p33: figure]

# Pipe Mapping via a Pass Through IMU-Based System

# Adison Heathcott Caleb Thorne Benjamin Ask Elizabeth Russell

### Tennessee Technological University

## Goal of the Project

The goal of this project is to create a probe that can be guided through a length of pipe and collect positional data. This data will then be uploaded to a computer, which will receive, process, and plot the collected data to create a map of the pipe system.

## Overall Design

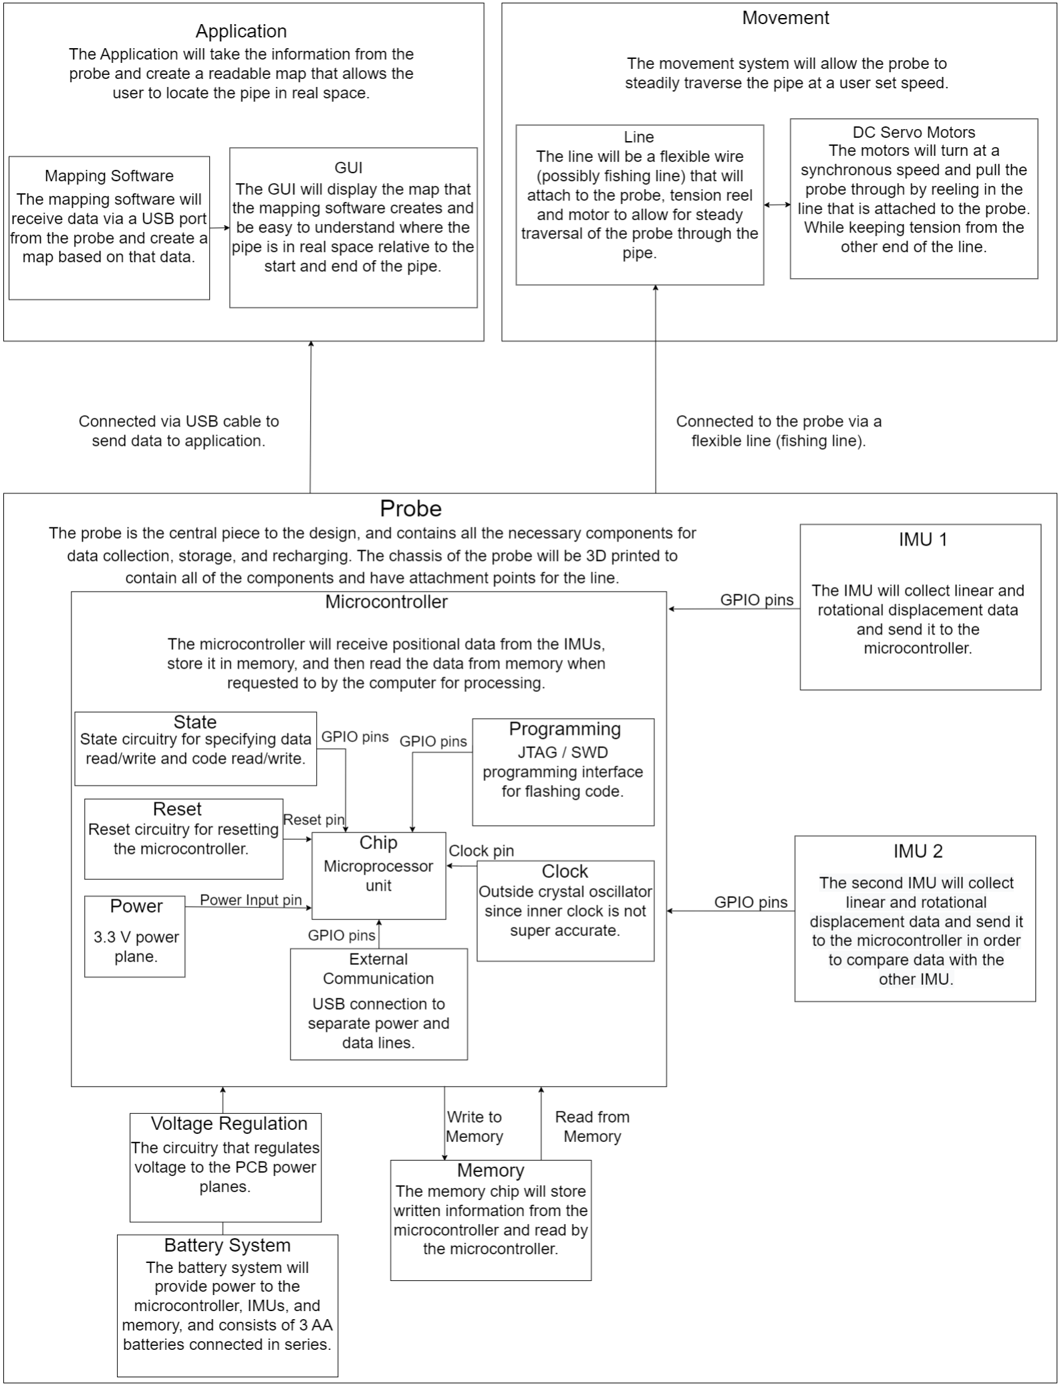
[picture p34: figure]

Figure 1. Block Diagram

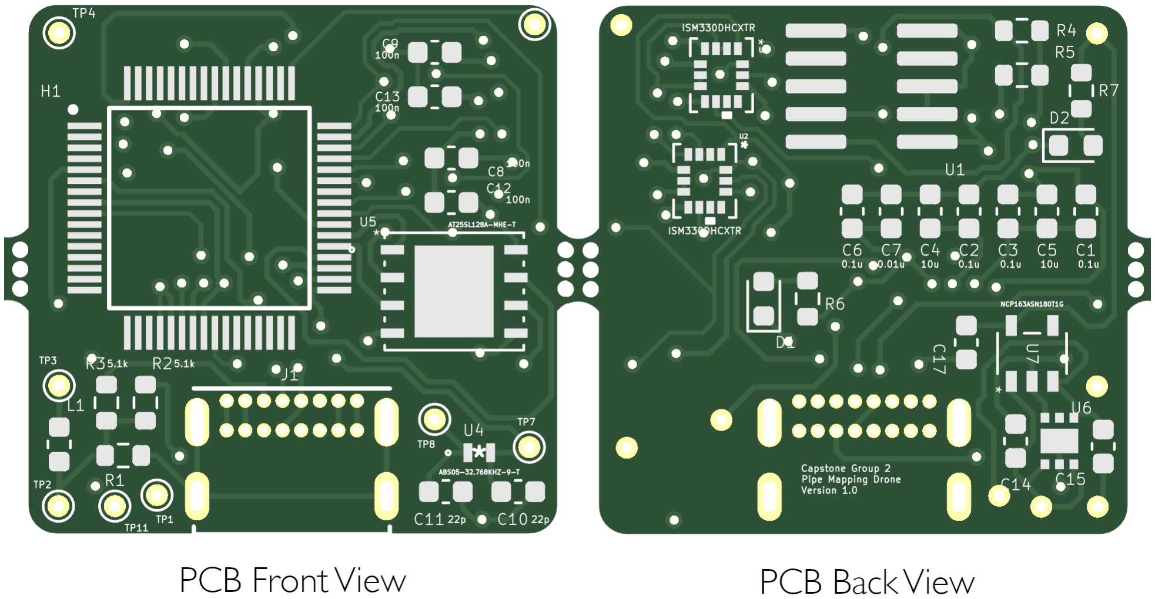
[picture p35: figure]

Figure 2. Initial PCB


Figure 3. Probe Casing

The initial probe casing design shows the PCB case on the right and the battery casings follow it. Eyelets screwed end to end allow the casings to be tied together via fishing line and wrapped around the motor spools for testing.

## Software

The software uses 3-axis position data from the accelerometer and 3-axis rotation data from the gyroscope to map a 3D path. The algorithm uses dead reckoning to map the data, which utilizes integration and Euler angles to calculate position across time. In addition, the software plots the ground truth in contrast to the calculated path and displays the distance between the endpoints.

## Testing

The testing of the mapping system was done by guiding the probe along a line taped to the floor and wall of the capstone lab, followed by measuring the accuracy of the positional data against the ”true position” of the pipe.

The memory was tested by collecting data for 20 minute intervals and checking to ensure that the memory was not full after that length of time.
The battery life was tested by measuring the initial battery voltage, then letting the system run for 20 minutes and measuring the battery voltage to calculate the total loss of charge. The load current of the probe was also measured, and was verified to be within an acceptable range.
The mapping system was tested by gathering data from the probe, and comparing the resulting map with the physical path that the probe was guided on.
The movement system was tested by pulling the battery casing through a 24 foot length of pipe while measuring the instantaneous velocity to ensure that it had minimal deviation throughout the run.

## Results


Figure 4. Plotted Results vs Ground Truth

The results show that the current implementation does not meet the initial specifications of being within 1” of the original pipe. However, it does give a general idea of the original pipe within an acceptable degree. After performing various tests to find the source of the error, the team has found a few sources.

Firstly, many subsystems had to be redesigned during implementation to fix errors in the initial design. Due to this the system was not able to fit into a pipe or the casing, so while the data was still obtained through valid methods, it was not the originally intended design. Secondly, natural error obtained from dead reckoning was compounded as the experiment was performed. While this error is not supposed to be significant, and the software helps to mitigate some of the error, it can not be ignored.

The results of the current design experiments show that the redesign in worth pursuing and would most likely give better results.

## Future Work

The probe has many improvements that were realized after implementation. Firstly, the system could be greatly simplified by using an Arduino Nano instead of an NXP microcontroller. Secondly, replacing the 6-axis IMUs with 9-axis IMUs can assist the probe in providing more accurate results.

The PCB was redesigned to fit on top of the Arduino Nano and to connect through the GPIO pins. The IMUs and memory were placed onto the new board and connected to the respective GPIO pins for SPI communication. Two LDOs were added to regulate the power from the batteries to the various subsystems.


Figure 5. Redesigned PCB

## Acknowledgements

The team would like to thank the ECE Department and Jesse Roberts for their assistance in this project. A special thank you to Mr. Conard Murray for his time, assistance, and advice through the entire process.

Another mention to xioTechnologies for supplying their open source software for mapping IMU data. https://github.com/xioTechnologies/Gait-Tracking

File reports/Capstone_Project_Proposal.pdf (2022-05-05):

# Pipe Mapping in 3D Space Proposal

Benjamin Ask
Department of Electrical and Computer Engineering Tennessee Technological University Cookeville, United States
baask42@tntech.edu

Caleb Thorne
Department of Electrical and Computer Engineering Tennessee Technological University Cookeville, United States
mcthorne42@tntech.edu

Adison Heathcott
Department of Electrical and Computer Engineering Tennessee Technological University Cookeville, United States
ayheathcot42@tntech.edu

Elizabeth Russell
Department of Electrical and Computer Engineering Tennessee Technological University Cookeville, United States
errussell42@tntech.edu

Abstract—For hundreds of years pipe systems have been used around the world to transport important resources over large distances. Today, the need for finding these old buried pipe systems is ever-growing as infrastructure continues to expand. Industrial pipe detection and location in the past, such as total stations, RTK, and LiDAR, have been the standard for many years. Recently, advances have been made to more efficiently locate these larger infrastructure networks, but residential pipe mapping has remained primitive. This paper assesses the current methods for residential pipe mapping and proposes a new method that is both cheaper and more efficient.
Index Terms—Capstone Design, Pipe Mapping, Residential Pipes, 3D Mapping
I. INTRODUCTION
Since the beginning of the 1700’s the United States has been laying an infrastructure of piping across the nation to supply essential resources, such as water and gas, to commercial, government, and residential buildings. In December of 2021 the government announced a $2.9 billion infrastructure bill that will replace all residential lead pipes with copper pipes. This imposes the question of how maintenance crews will find already existing pipe networks at a low cost without the danger of heavy digging equipment.
Currently, methods exist for the detection of large industrial pipes but there is a lack of such technology for small residential pipes. This document proposes a new way of mapping pipe networks using a small probe to record depth and location information while harmlessly traversing the pipe. The team’s objective is to create a probe based system to traverse and map variable sized underground pipe networks in 3D space within an acceptable margin of error. While implementing the mechanical traversal of the pipe is not within the scope of this project, the primary goal consists of setting up the base technology for 3D mapping and real time information transmission inside a pipe.
The structure of this paper is as follows. The background of current detection and location methods, in both industrial and residential environments, will be discussed in more detail in Section 2. The constraints and specifications of the team’s proposed method will be discussed in Section 3. Section 4 will expand on the current obstacles seen by the team with the given constraints and will discuss how the team will be measuring success with each experiment as well as the entire project. The relevant standards, broader impacts, and ethical considerations will be discussed in Section 5, and Section 6 will cover the timeline and required resources established by the team.

II. BACKGROUND

To understand why a new method for pipe mapping is greatly needed it is first necessary to understand the current methodologies. While piping has been around since early recorded time the methods for finding buried pipe networks have largely been neglected. In recent years accomplishments in pipe detection and location have been made, however, they still lack the cost effective and ease of use that many technologies today offer. In this section an overview of current pipe location methods in both industrial and residential contexts is discussed. Further analysis on the safety and cost implications of both methods is explored in more detail.

A. Current Industrial Pipe Locating Methods
Industrial Pipe locating is an important technology for infrastructure expansion and repair leading it to be the more researched domain. Previous methods included total stations, real-time kinematic positioning (RTK), and light detection and ranging (LiDAR). New research in inertial mapping has led to advances that create a 3D model through the detection of pipes ranging in diameters from 29-34mm to 90-1500mm for distances of up to 2 km with a precision of up to 15 cm in XYZ space [1]. While these are helpful they suffer from the inability to find cross-bores (natural gas lines that intersect sewage lines) and cause unwanted pipe damage when excavating. Currently, the best methods for detecting pipes are by using electromagnetic wants (EMI) or ground penetrating radar (GPR) pushcarts. These methods lead to a safer and cheaper way of locating pipes but must be conducted at the time of installation. However, it remains a challenge to locate pipes installed with horizontal drilling using this method.
B. Current Residential Pipe Locating Methods
Residential pipe location is still very primitive and commonly requires large and dangerous equipment. If the pipe network cannot be established from the entry and exit point of the pipe wanted a grid search must be conducted on the property which can be time consuming and expensive. To better understand the implications of pipe location it is necessary to understand the contexts in which they are used. Pipe replacement is the most common reason one may need to find an underground pipe network. There are two main types of pipe replacement; trenchless and traditional.
Trenchless pipe replacement has two main types: pipe lining and pipe bursting. Pipe lining essentially lines the old pipe with epoxy-impregnated liner thus creating a new pipe inside the old. Pipe bursting replaces an old pipe by taking a new highdensity polyethylene (HDPE) pipe and pulling it through. The old pipe busts the old into pieces and replaces it in the same location. This is effective for longer pipes but has limitations for anything that is not a straight horizontal pipe. Traditional pipe replacement is the most common method and requires the need to dig through various materials that may be covering the pipes.
Even though trenchless pipe replacement can be used to avoid digging and locating pipes the problems and cost are still large enough to consider another method.
C. Safety and Cost
Both residential and industrial pipe location can be extremely time consuming and expensive and can require dangerous machinery to access the network. For an individual the equipment and expertise may be hard to acquire. For a business it may be difficult to hire a contractor in time to use the equipment needed and may extend or jeopardize the success of the job in a timely manner.
Trenchless pipe replacement cost depends on the methods used. If pipe lining is used a rough cost of $80 - $250 per foot is standard with an average of $160. For a complete pipe replacement in a standard home the range is $6,000 - $12,000. If pipe bursting is used a rough cost of $60 - $200 per foot is standard. A complete pipe replacement can cost upwards of $3,500 - $20,000. [2]
Traditional pipe replacement cost can vary depending on the success of pipe location. The following data assumes that the pipe was found on the first attempt of excavation. The average cost to dig and replace a pipe is $50 - $250 per foot. A small pipe replacement can be $3,000 - $6,000 and can increase to $5,000 - $13,000 for repairs longer than 50 feet. The cost of replacing sod, landscaping, concrete and labor contribute to the cost as well.
When looking at the CAT rental store [3] the necessary tools for underground pipe installation include an excavator, trencher, trench shoring equipment, pipelaying underground laser, pipelayer, and compactor. The cost of this equipment is estimated to be $1,574 per day and could be more expensive depending on the job. One of the most important costs to evaluate is the injury or death of one or more persons during these practices.
One of the most important costs to evaluate is the injury or death of one or more persons during these practices. With the extended use of heavy machinery and hydraulic equipment there is a possibility of injury or death. Using the method in this proposal, the team aims to lower the cost and liabilities of pipe related jobs by more effectively and safely locating pipe networks.

III. CONSTRAINTS AND SPECIFICATIONS

With a background on pipe replacement methods and the cost of trench digging one can now understand the basic constraints and specifications that may be considered by the design team. The specifications are constraints held by the team, and stakeholders, that will help define success or failure. The constraints are defined by standards and physical limitations on the design. This section will discuss the specifications needed by the team and possible users of the technology and constraints defined by standards and physical limitations.

A. Specifications
The current methods of pipe location can be costly and dangerous. As such, the largest specification for the project is to lower cost and decrease heavy machinery use by accurately providing pipe network mapping. Retrievability and reusability will be paramount in ensuring the cost and benefits remain at a level where the technology will be worth using. Retreivability will be maintained by the use of a string that will be used to guide and move the probe through the network. Reusability will be maintained by the ability to reset the probe memory state every time it needs to be reused. Specifications will be designed to take potential users and government and organization standards in to account.
B. Constraints
The environment in which the probe will be operating is a 1” to 4” in diameter pipe network that has 90° turns and complex piping structures. This defines a constraint for small and flexible electronics and the need for a transmission domain that can penetrate the PVC and possible materials surrounding the network.
The probe size should not pose a problem due to the availability of extremely small sensors and PCBs. The method that the team plans to use to avoid problems with 90° turns is splitting the probe into modules so the bending and turning of circuit boards and sensors will not be an issue.
The constraints for this project have been well thought out and will not pose a problem in the team’s final design.

IV. SUCCESS MEASUREMENTS

Success must be measured to account for abnormalities in testing and inevitable error, however, it must also meet strict standards that adhere to statistically informed specifications.

The team’s success is split up into multiple sections to better and more accurately determine if the system operates correctly and meets specifications. The experiment designed by the team takes into account each of the sections listed below. The device will be run through 10 different PVC pipe networks using a rope attached to the device pulling it through. 10 trials will be run on each of the networks that are built to test for accuracy, speed, and battery life. Using the data that will be collected from these trials, an accurate measurement of the success rate and therefore overall success of the build can be generated.

A. Mapping Accuracy

The device will need to map the pipe that it is traversing within a reasonable margin of error. The test will be considered a success if it can accurately map a pipe network within a 1” radius of the actual network.

B. Mapping Speed

The device will need to be tested for the appropriate speed at which it can accurately retrieve data and still be efficient. Successful efficient speed will be acquired if the probe can move at least 6 in/sec and still obtain accurate data.

C. Battery Life

Battery life of the device is especially important as it would be inefficient be unable to map an entire pipe in one charge. Battery life will be considered a success once the device can map at least 1000 feet of pipe on one charge / battery replacement.

D. Cost

The cost of the device must be justified by keeping the value added higher than the cost of the device. This will be calculated as the team designs and tests the build. If each of the previous categories are satisfied within a reasonable cost the cost will be considered a success.

V. STANDARDS, IMPACTS, AND ETHICS

There are many standards that this project will need to adhere to, most of which have been set forth by either professional standards organizations or federal agencies. These standards will act as constraints that will enable the design of a safe and effective final product.
Alongside the relevant standards, there are numerous externalities that must be considered throughout the design process and implementation of the proposed pipe mapping system. While some of the possible externalities are quickly identifiable from the beginning, some may only become apparent throughout the course of the project, and will likely vary as the specific design changes.
A list of standards relevant to this project are listed in the corresponding subsection below, followed by a more focused look at some of the possible externalities.
A. Relevant Standards
- National Electric Code (NEC)
– Article 460: Capacitors
– Article 470: Resistors and Reactors
– Article 480: Storage Batteries
- Environmental Protection Agency (EPA)
– Mercury-Containing and Rechargeable Battery Management Act
- Federal Communications Commission (FCC)
– 47 CFR 15: Radio Frequency Devices
- Institute of Electrical and Electronics Engineers (IEEE) – 1293: IEEE Standard Specification Format Guide and Test Procedure for Linear, Single-Axis, Nongyroscopic Accelerometers
- IPC
– IPC-A-600: Acceptability of Printed Boards
– IPC-A-610: Acceptability of Electronic Assemblies
B. Externalities and Ethical Considerations
When considering the possible externalities that could stem from this project, one of the foremost concerns is the potential for the device to become lost, stuck, or otherwise irretrievable from the pipe system that it is mapping. An event like this not only poses a potential risk to the pipe network, and thus a risk to the property of the client, but also raises questions regarding the optimal method for data preservation in the event that the probe is recovered after such an incident.
The probe must also be constructed in such a manner that it will neither damage nor introduce potentially unwanted contaminants into the pipe network, whether during normal operation or in a failure case as described in the previous paragraph. This means that special care will need to be taken in regards to choosing the material making up the outermost surfaces, as well as properly protecting any potentially harmful chemicals contained within the device, such as battery acid. While PVC material is relatively resistant to such acid [4], lead pipes are a different story.

VI. TIMELINE AND RESOURCES

The timeline of the project is a very rough estimate of times and objectives for each member, and the team as a whole, to meet. The resources are the collective abilities of each of the team members that will enable the team to complete the proposed project. In this section, a detailed specification for a brief timeline and resources necessary for the project will be discussed in depth.

A. Timeline
Currently the tasks are divided into their subsystems for the project and distributed to the most experienced team members in that area respectively. Benjamin Ask is working on the research and design of the storage subsystem. Caleb Thorne is working on the research and design of the transmission subsystem. Adison Heathcott is working on the research and


Fig. 1. Timeline Gannt Chart.

design of the mapping and tracking subsystems. Elizabeth Russell is working on the research and design of the power subsystem. “Fig. 1” shows the timeline in which the team expects to finish each of the subsystem checkpoints.

B. Personnel
This section summarizes the skills that each member of the team possess that will most likely be utilized during the designing, building, and testing of the mapping probe. These skills were also taken into heavy consideration when deciding what subsystems each member would handle.

Caleb Thorne
- PCB Design
- Telecommunication
- 3D Modeling
- Prior knowledge of power systems
- Matlab

Benjamin Ask
- Prior knowledge of piping work
- Matlab
- Digital Logic Design
- Embedded Systems
- C++ / C

Adison Heathcott
- PCB Design
- Embedded Systems
- Digital Logic Design
- Matlab
- C++ / C

Elizabeth Russell

- Matlab
- Labview
- Electromagnetics
- Telecommunication
C. Resources

The necessary equipment, average cost per item, software, and total estimated cost of the mapping probe are compiled in “Table. I”. The expected cost was determined by calculating the average of the most cost efficient and advanced models of the parts. This equipment is essential as the theoretical design of the probe consists of four modules: transmission, mapping / tracking, power, and memory storage. To implement the transmission module a transceiver will need to be utilized, tracking and mapping will use a gyroscope and Matlab, power will use batteries, and the storage module will vary in type and amount of memory depending on the project needs.

D. Required Equipment and Software
- Battery
- Transceiver
- PVC
- Memory storage
- Gyroscope
- Matlab
- Labview
- C++
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

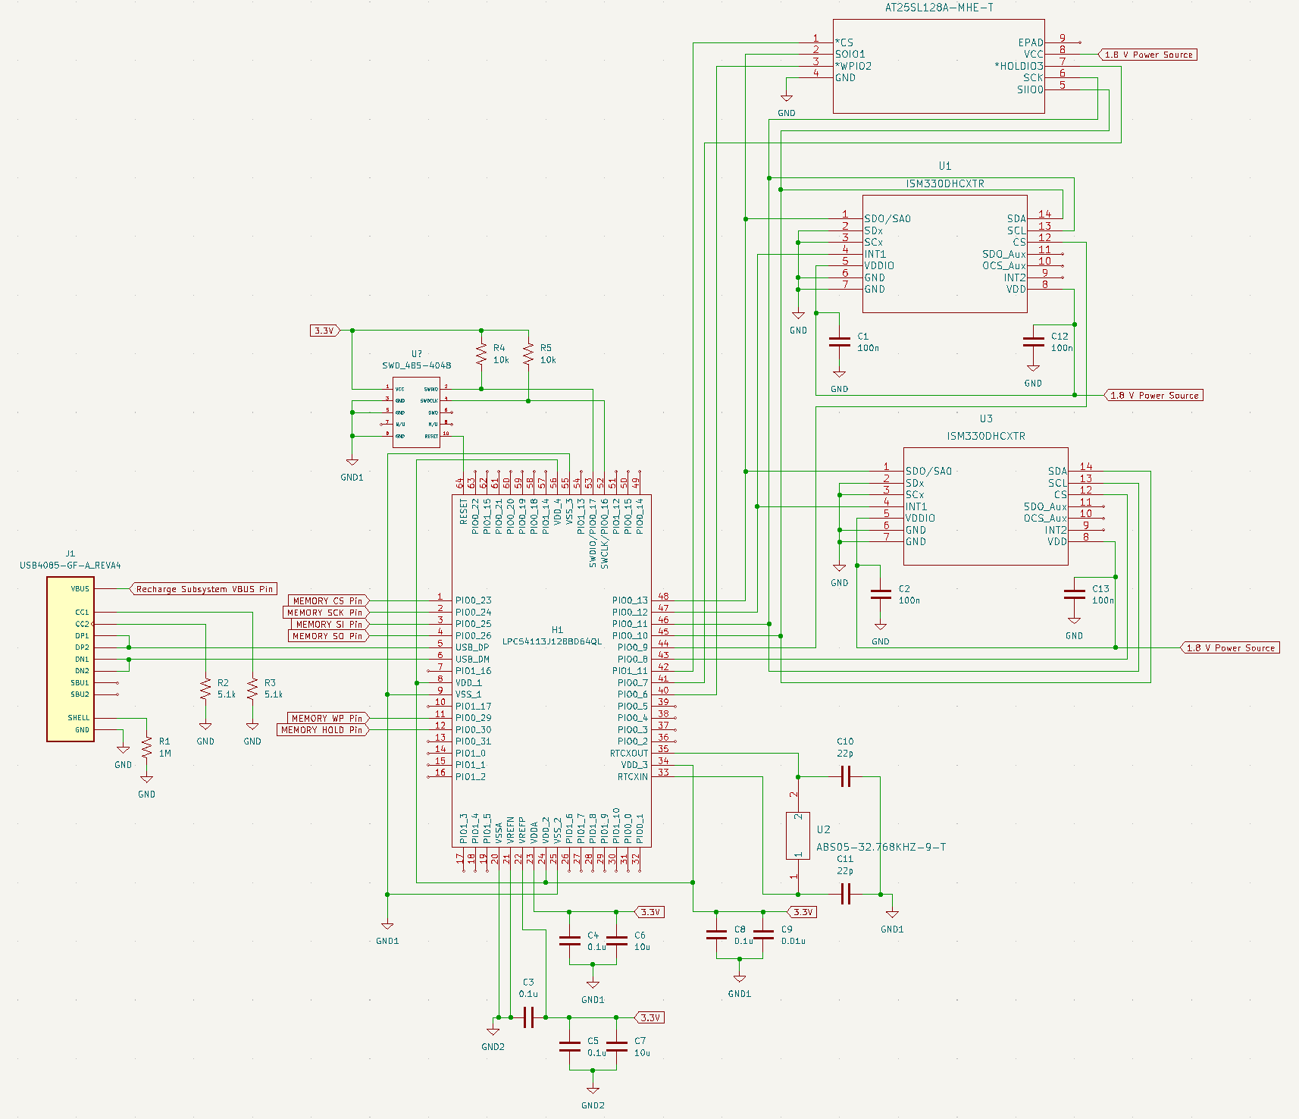
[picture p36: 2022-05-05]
projectDocumentation/memorySubsystem/Memorytotalschematic.png

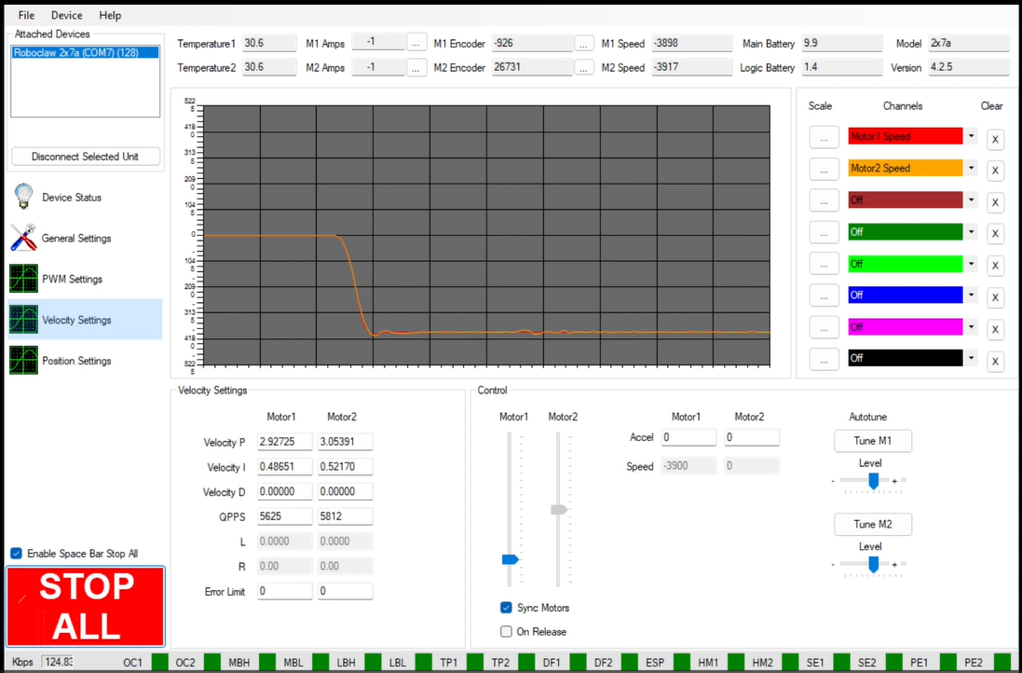
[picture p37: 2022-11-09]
projectDocumentation/motorControllerSubsystem/run2graph.png

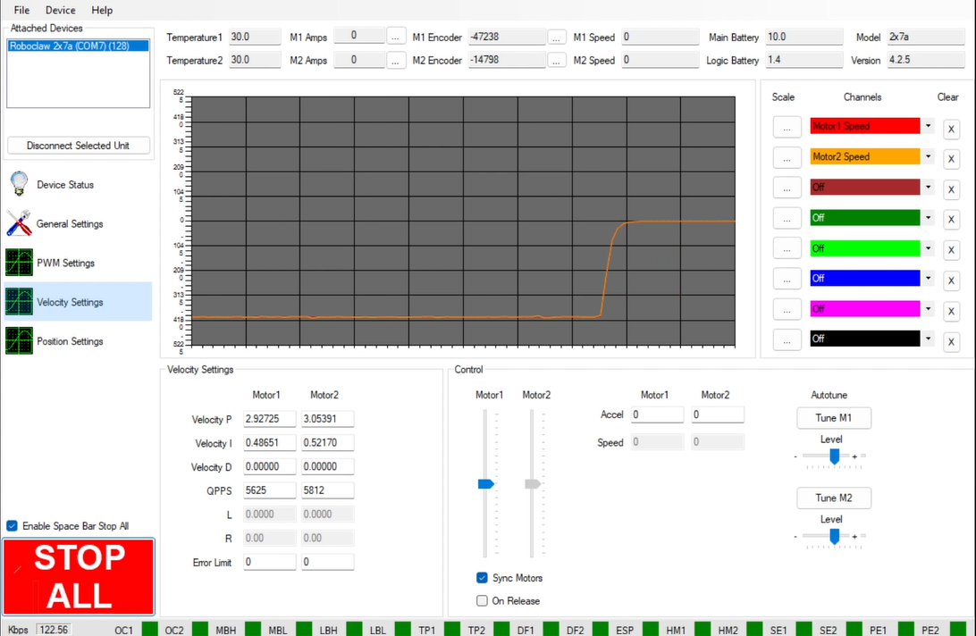
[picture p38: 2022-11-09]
projectDocumentation/motorControllerSubsystem/run4graph.png

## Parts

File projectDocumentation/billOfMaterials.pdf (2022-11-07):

Name of Item | Description | Used in which subsystem(s) | Part Number | Manufacturer | Quantity Price | Total
IMU's | 6-Axis Inertial Measurement Units Data Collection | ISM330DHCXTR | STM | 2 | 11.34 22.68
MCU | Low Power 32-bit Microcontroller Data Collection | LPC54113J128BD64QL NXP Semiconductors | 1 | 8.41 | 8.41
Memory Chip | 128 Mbit Flash Memory | Data Collection | AT25SL128A-MHE-T | Adesto Technologies | 1 | 2.19 | 2.19
1.8V LDO | 1.8V Voltage Regulator | Power | NCP163ASN180T1G | ONSEMI | 2 | 0.52 | 1.04
3.3V LDO | 3.3V Voltage Regulator | Power | NCP711BMT330TBG | ONSEMI | 2 | 0.9 | 1.8
PCB | The printed circuit board | PCB | PCB | JLCPCB | 1 | 52.72 52.72
1.0 uF Capacitor | PCB capacitor | PCB | 885012106022 | WurthElektronik | 6 | 0.43 | 2.58
0.1 uF Capacitor | PCB capacitor | PCB | 88502206020 | WurthElektronik | 16 | 0.1 | 1.6
0.01 uF Capacitor PCB capacitor | PCB | C0603X103F3GACTU | KEMET | 2 | 2.05 | 4.1
10 uF Capacitor | PCB capacitor | PCB | AEF0608100M100R | Kyocera AVX | 4 | 0.6 | 2.4
22 pF Capacitor | PCB capacitor | PCB | C1608C0G1H220J080AA TDK | 4 | 0.12 | 0.48
Red LED | Red status LED | PCB | AA1608SURSK | Kingbright | 2 | 0.54 | 1.08
60 Ohm Resistor PCB resistor | PCB | RG1608N-680-W-T1 | Susumu | 2 | 0.8 | 1.6
10 kOhm Resistor PCB resistor | PCB | RG1608N-103-W-T5 | Susumu | 4 | 0.76 | 3.04
Resistor Kit | PCB resistors | PCB | 1222680 | MCIGICM | 1 | 7.99 | 7.99
Motor | 12 V Metal Gear Motor | Mechanical | 4865 | Pololu | 2 $45.95 | 91.9
Motor Bracket | Pololu 25D mm Motor Bracket | Mechanical | 2676 | Pololu | 1 | $7.95 | 7.95
Motor Controller Roboclaw 2x7A Motor Controller | Motor Controller | IMC404 | BASICMICRO | 1 $79.95 | 79.95
Battery Holder | AA Battery Holder with Lead Wires Power | 6543877239 | LampVPath | 1 | $6.48 | 6.48
Super Glue | Loctite Super Glue Ultra Gel | Mechanical | 1739050 | Loctite | 1 | $4.36 | 4.36
Fishing Line | Clear Fishing Wire, 656 ft | Mechanical | AFL-05 | Acejoz | 1 | $6.65 | 6.65
PVC Pipe | 20ft 2" schedule 40 pvc | Mechanical | 72000800 | Charlotte | 2 $43.82 | 87.64
PVC 90 | Nibco 90 elbow pvc | Mechanical | 39923215543 | NIBCO | 10 | $5.15 | 51.5
AA Battery | 28 Duracell AA batteries | Power | B08Q87MF19 | Duracell | 1 $14.69 | 14.69
| | | | | | | 0
Total | Total Components | 70 Total Cost 464.83

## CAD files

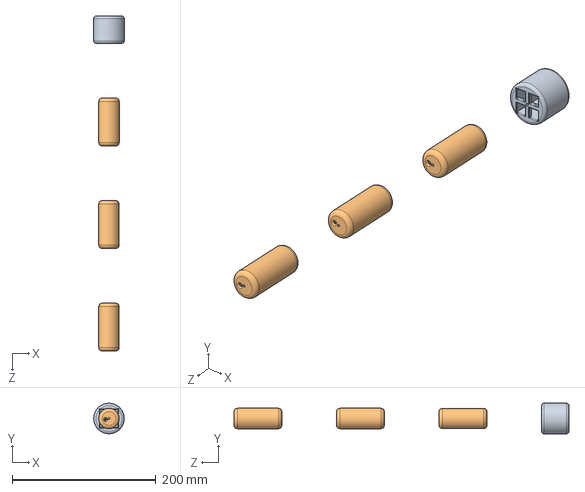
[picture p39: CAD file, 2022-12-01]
projectDocumentation/probeCasingSubsystem/ProbeCasingAssy.SLDASM
42.6 x 42.6 x 466.6 mm
PCB Carrier
Battery Carrier x 3

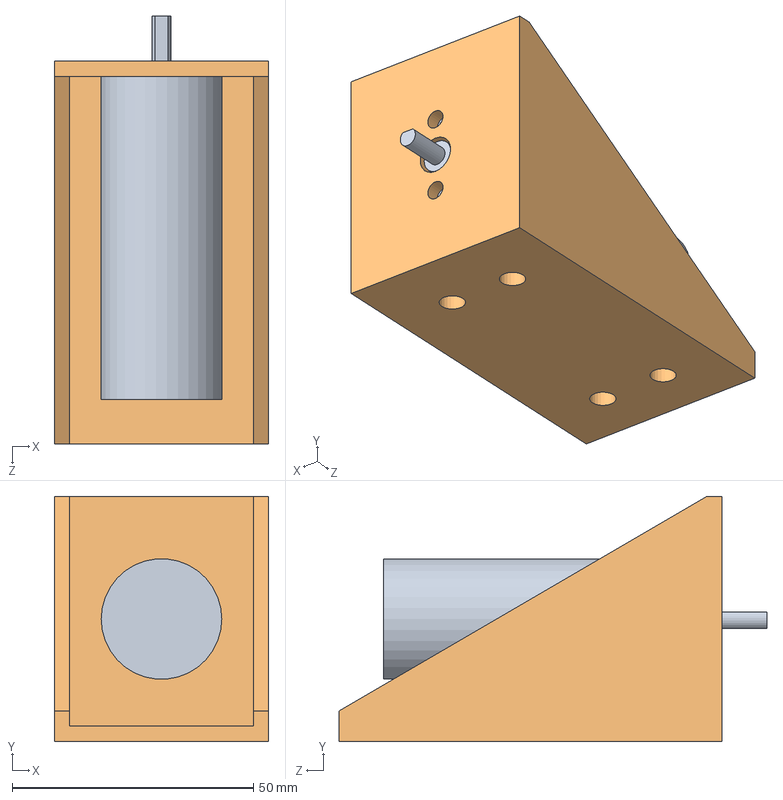
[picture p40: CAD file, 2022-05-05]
projectDocumentation/mechanicalSubsystem/SolidWorks/MotorAssy.SLDASM
44.5 x 50.8 x 88.7 mm
Motor Model
Motor Mount

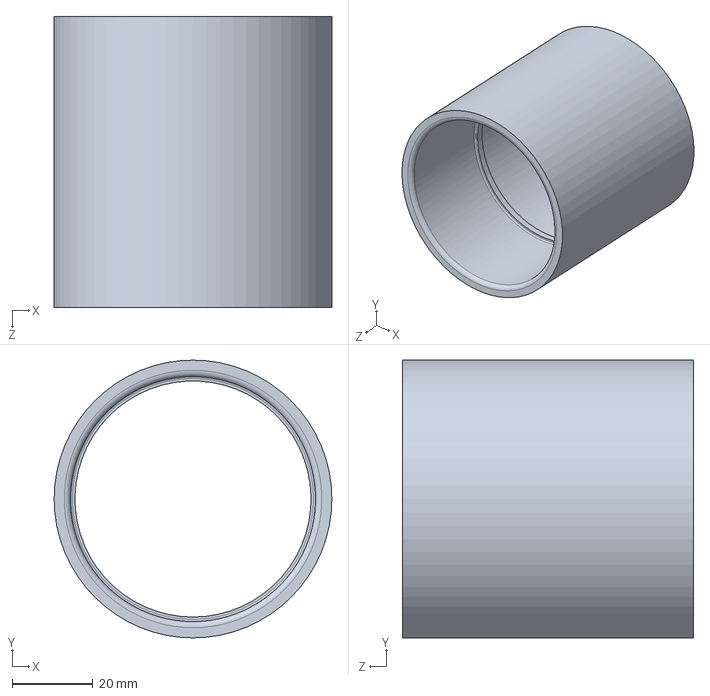
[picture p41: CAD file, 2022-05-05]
projectDocumentation/mechanicalSubsystem/SolidWorks/PVC90.SLDPRT
68.7 x 68.7 x 72.0 mm

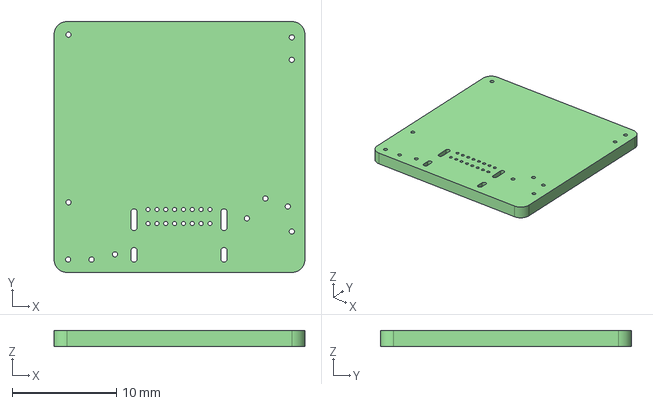
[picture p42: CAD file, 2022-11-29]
projectDocumentation/pcbSubsystem/KiCAD_PCB_Design/Capstone.step
24.1 x 24.1 x 1.55 mm

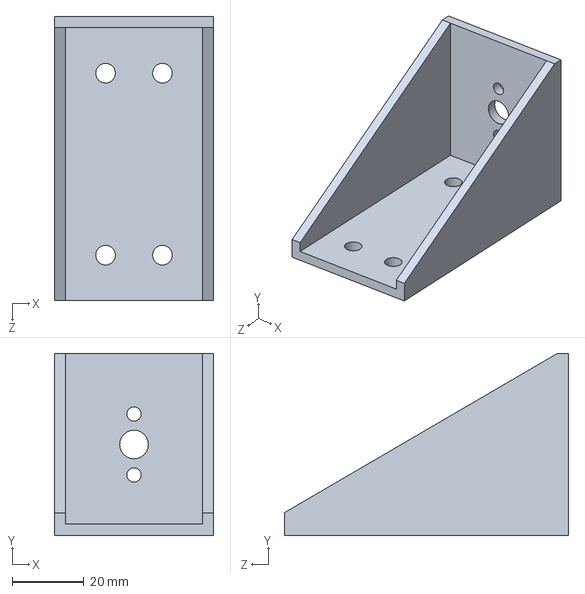
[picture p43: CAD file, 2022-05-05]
projectDocumentation/mechanicalSubsystem/SolidWorks/MotorMount.SLDPRT
44.5 x 50.8 x 79.4 mm

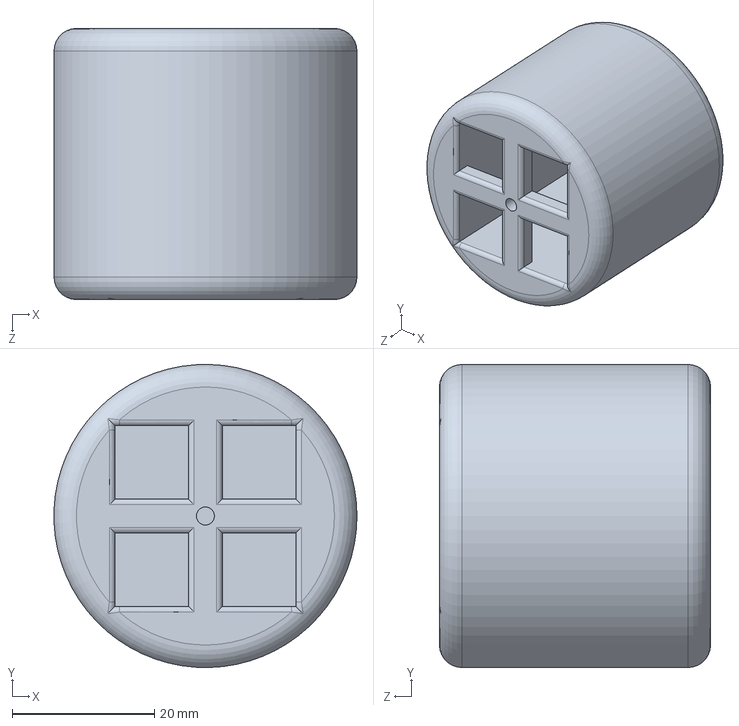
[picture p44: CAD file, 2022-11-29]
projectDocumentation/probeCasingSubsystem/PCB Carrier.SLDPRT
42.6 x 42.6 x 38.1 mm

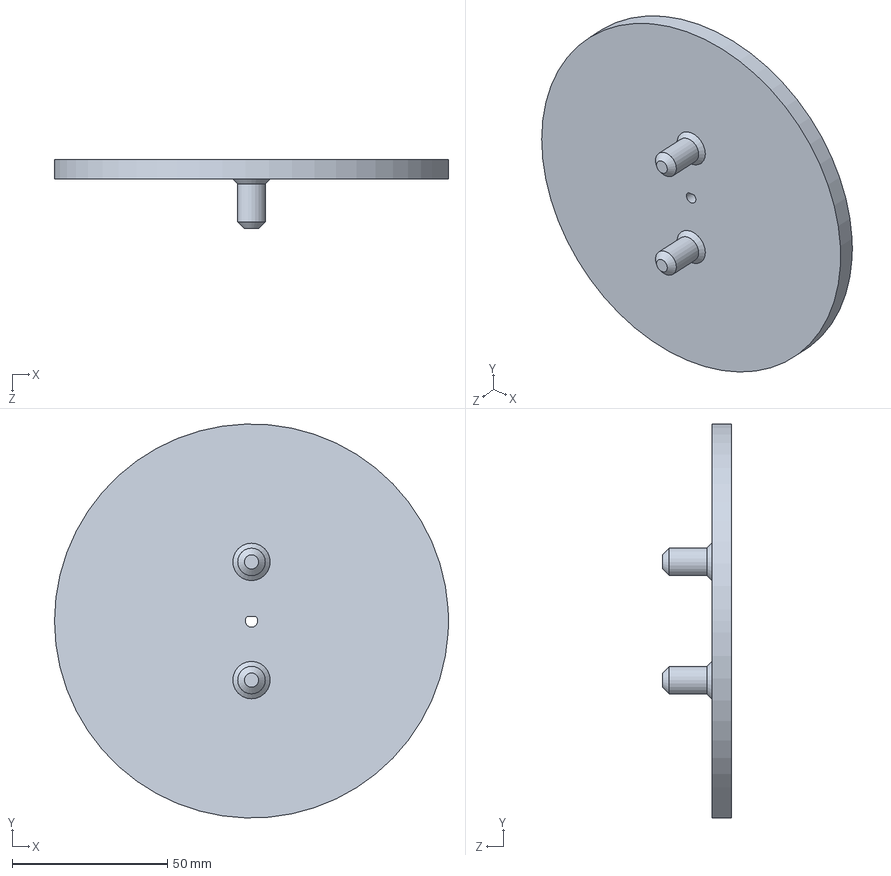
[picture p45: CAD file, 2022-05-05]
projectDocumentation/mechanicalSubsystem/SolidWorks/SpoolPt2.SLDPRT
127.0 x 126.9 x 22.2 mm

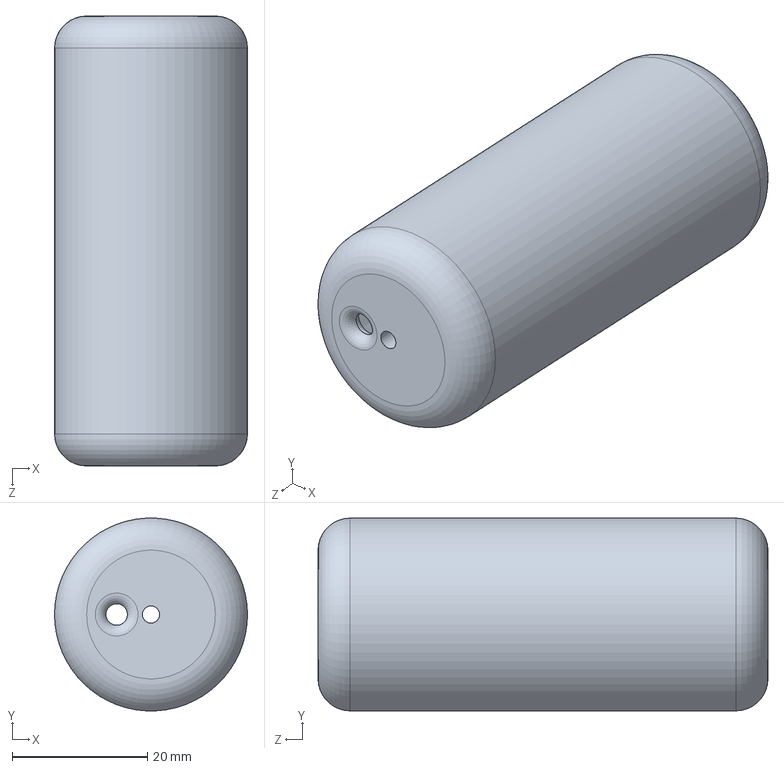
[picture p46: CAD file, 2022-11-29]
projectDocumentation/probeCasingSubsystem/Battery Carrier.SLDPRT
28.6 x 28.5 x 66.6 mm

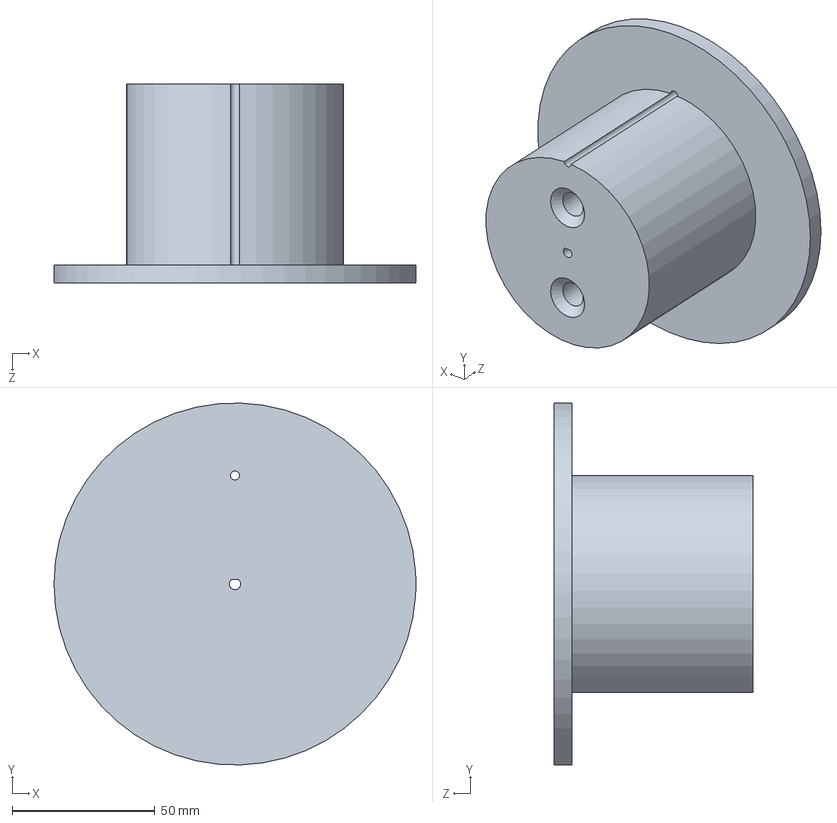
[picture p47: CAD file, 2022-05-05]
projectDocumentation/mechanicalSubsystem/SolidWorks/SpoolPt1.SLDPRT
127.0 x 126.9 x 69.8 mm

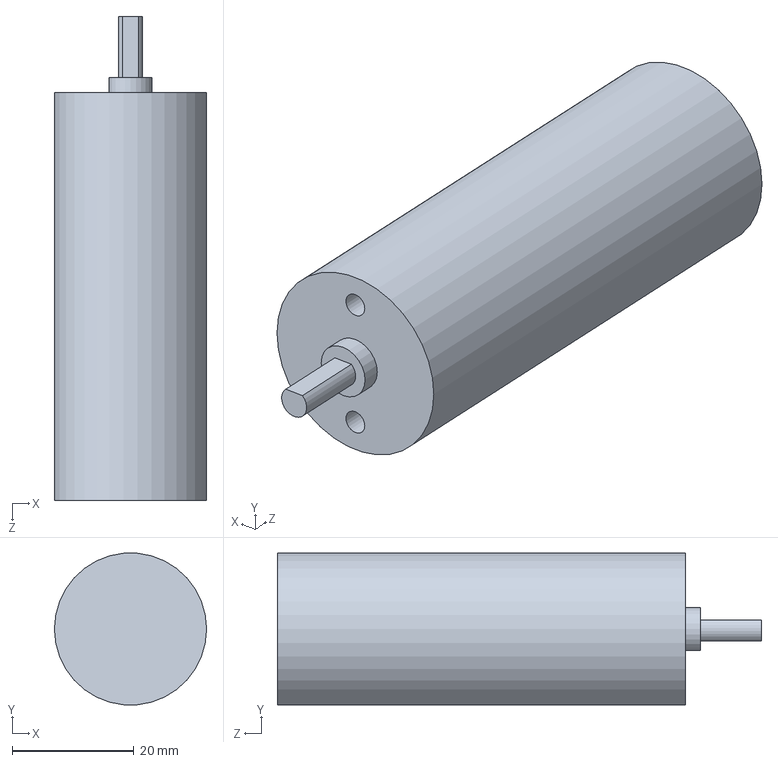
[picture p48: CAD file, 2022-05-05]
projectDocumentation/mechanicalSubsystem/SolidWorks/MotorModel.SLDPRT
25.0 x 24.9 x 79.5 mm

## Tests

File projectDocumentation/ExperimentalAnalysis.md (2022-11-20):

# 3D Pipe Mapping Probe: Experimental Analysis
## Experiment 1
The first experimentation we did was on the mechanical subsystem which includes the motors, pipe network, and spool with fishline. The completed experiment consisted of a "dummy" battery holder shell being pulled through the 24 foot long 2 inch diameter PVC network. While the probe was being pulled through we kept a running graph of the instantaneous motor velocity and found the largest difference between the desired velocity and the actual velocity of the motor (data shown below). Screenshots of the graphs have been provided below to show how the data was collected.
### Motor Velocity Graph
#### Run 1 Mid Pipe Snapshot

#### Run 2 Beginning Pipe Snapshot

#### Run 3 Beginning Pipe Snapshot

#### Run 4 End Pipe Snapshot

#### Run 5 End Pipe Snapshot


### Motor Velocity Deviation Table
| Run Number |Set Velocity (ft/sec) | Maximum Velocity Deviation (ft/sec) |
| --- | --- |---|
| 1  | 1.39  | 0.016 |
| 2  | 1.36  | 0.060 |
| 3  | 1.34  | 0.038 |
| 4  | 1.41  | 0.019 |
| 5  | 1.27  | 0.052  |

### Analysis & Recommended Improvements
One problem that we encountered with this system is that while the battery shell easily traversed the network, the PCB shell often got stuck in the 2" 90 degree elbows due to a small lip that was not forseen in our initial design. Our next step is to redesign the PCB shell to have a more gradual edge rather than being very nearly a perfect cylinder. It is likely that both the battery shell and PCB shell would fit in a larger diameter PVC system but our cost for testing would have had to be much higher to confirm that theory. What this experiment verified was that our mechanical subsystem pulls at or above our minimum velocity (1 ft/sec) and pulls consistently with very little deviation so as to minimize the error during data collection. While we did not have a specific number constraining our velocity deviation we found that the deviation was always less than 0.1 ft/sec in each of our five tests which means if we run our probe around 1 ft/sec then we will never exceed our maximum velocity of 2 ft/sec which was calculated based on our sampling rate. Therefore this system successfully remained within the constraints while meeting specifications.

## Experiment 2
The second experiment was designed to test the accuracy of the probe and to see if the data measured produced data within our specifications. Our constraints define a successful plot to be within a 1" radius of the measured pipes edge. 

For the following iterations of the experiment, it was not possible to measure the probes location from inside a 2" pipe. Instead, the probe was run over four separate paths defined by duct tape on the floor and walls. For each of the experiments it is assumed that the start location of the probe is (0, 0, 0) on a 3D axis defined as (x, y, z) and the probe is facing the positive y direction.

### Experiment Iteration 1

For the first iteration the tape line is plotted as the orange line on the graphs, however, a text description is included here as well. The first run consisted of a straight line exactly 6.14 meters long. The second run consisted of a straight line for 3.35 meters, a right turn, and another straight line for 3 meters. The third run consisted of a straight line for 2 meters, a turn upward, and a straight line for 4.14 meters. The fourth run consisted of a straight line exactly 2 meters in length.

The graph below shows the network number and run number for each experiment, the sample rate the data was captured at, the threshold value set in the software, and the final point of the measured data minus the final point of the baseline. The threshold value is set in the software and defines the minimum normalized acceleration that would constitute the probe as "moving". The difference of the final points is represented as (x, y, z) with each value being the distance between the two points on their respective axis.

| Network Number & Run Number | Sample Rate (Hz) | Threshold | Measured vs Baseline Endpoint Difference |
| - | - | - | - |
| 1 - 1 | 26 Hz | 0.1 | (7.05, 6.16, 2.32) meters |
| 1 - 2 | 26 Hz | 0.1 | (4.98, 7.22, 1.02) meters |
| 1 - 3 | 26 Hz | 0.1 | (5.54, 1.18, 2.22) meters |
| 2 - 1 | 26 Hz | 0.1 | (0.41, 0.50, 2.72) meters |
| 2 - 2 | 26 Hz | 0.1 | (13.0, 21.4, 8.72) meters |
| 2 - 3 | 26 Hz | 0.1 | (13.3, 4.71, 4.76) meters |
| 3 - 1 | 26 Hz | 0.1 | (97.1, 5.70, 50.3) meters |
| 3 - 2 | 26 Hz | 0.1 | (10.7, 0.67, 2.18) meters |
| 3 - 3 | 26 Hz | 0.1 | (27.4, 4.14, 29.8) meters |
| 4 - 1 | 26 Hz | 0.1 | (87.9, 199.4, 612.3) meters |
| 4 - 2 | 26 Hz | 0.1 | (24.4, 73.1, 214.1) meters |
| 4 - 3 | 26 Hz | 0.1 | (18.3, 108.4, 183.8) meters|

It is difficult to represent the deviation through the path without having tables full of thousands of data points, so the graphs below show the baseline (orange) and the measured line (blue). The endpoints have been measured to give some metric of how far off the final values are, but the intermediate values need to be evaluated graphically. Note in some of the graphed simulations the orange line is difficult to see but it is there.


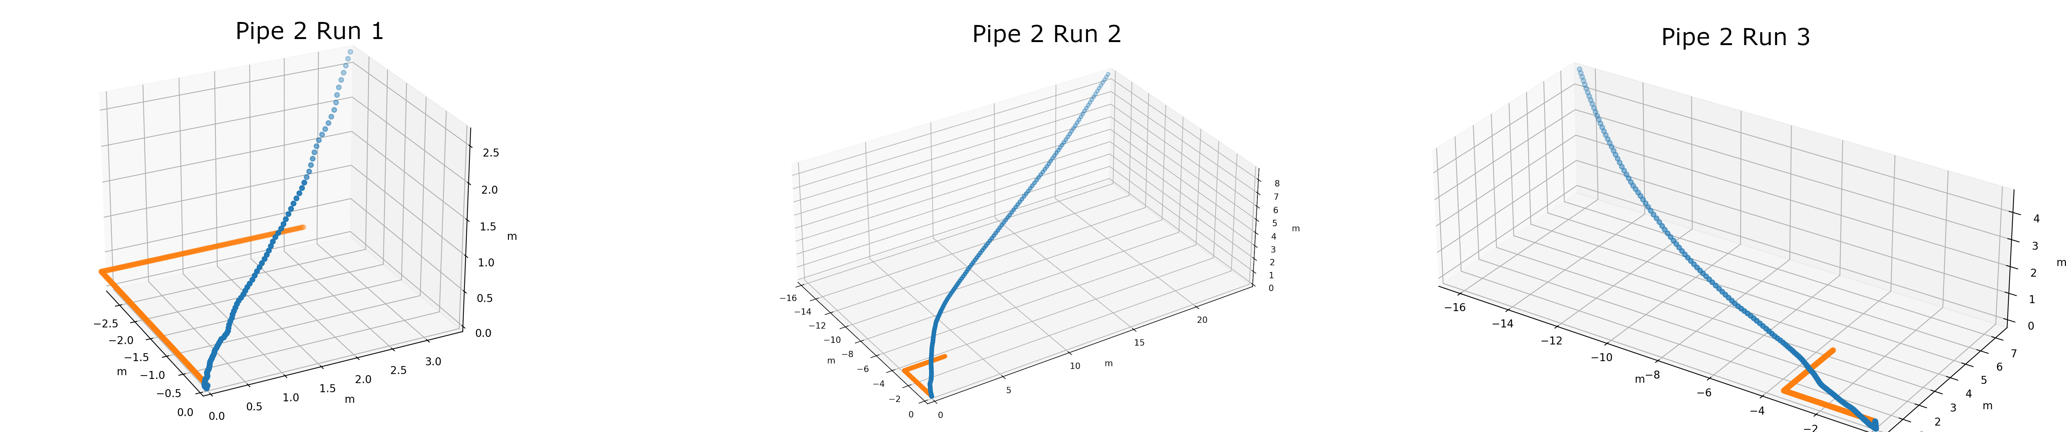
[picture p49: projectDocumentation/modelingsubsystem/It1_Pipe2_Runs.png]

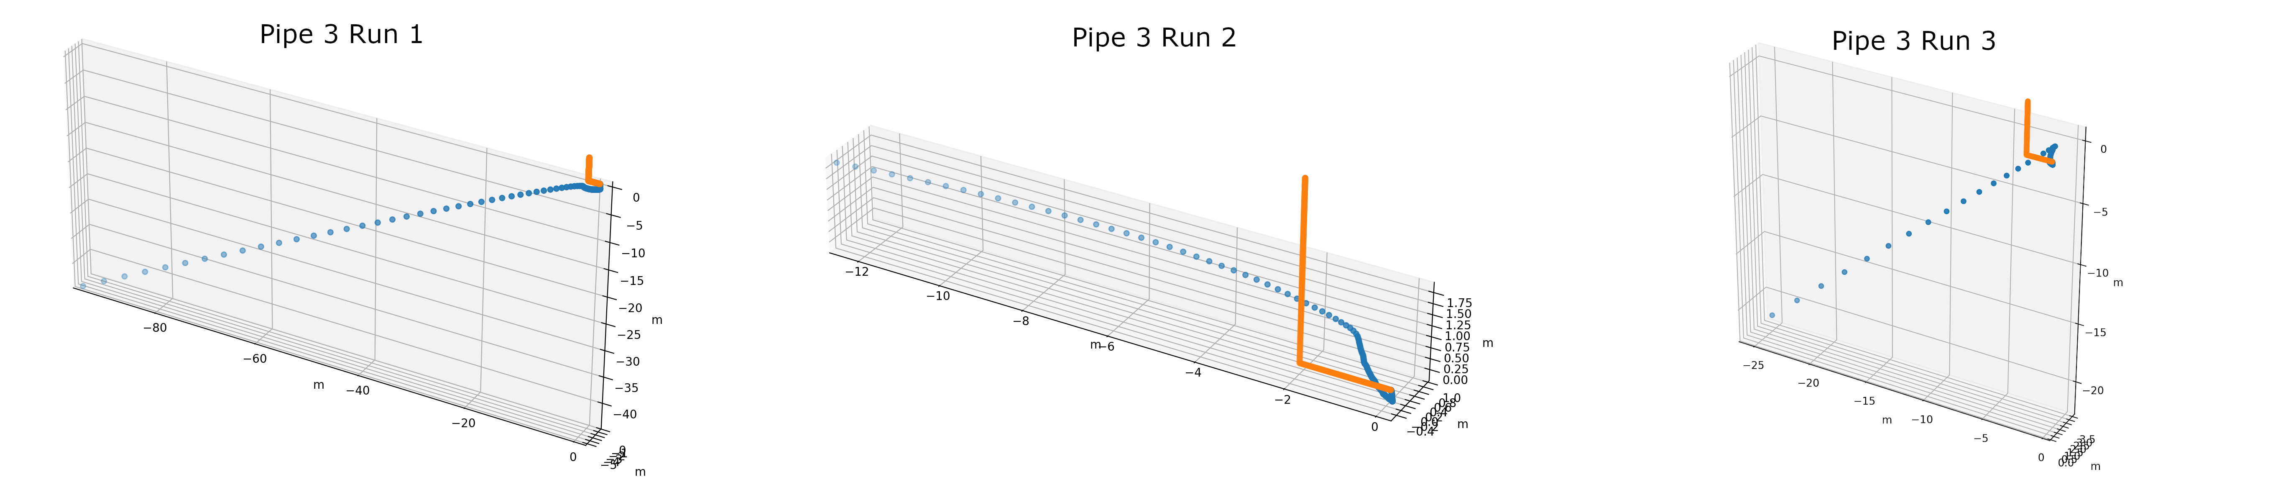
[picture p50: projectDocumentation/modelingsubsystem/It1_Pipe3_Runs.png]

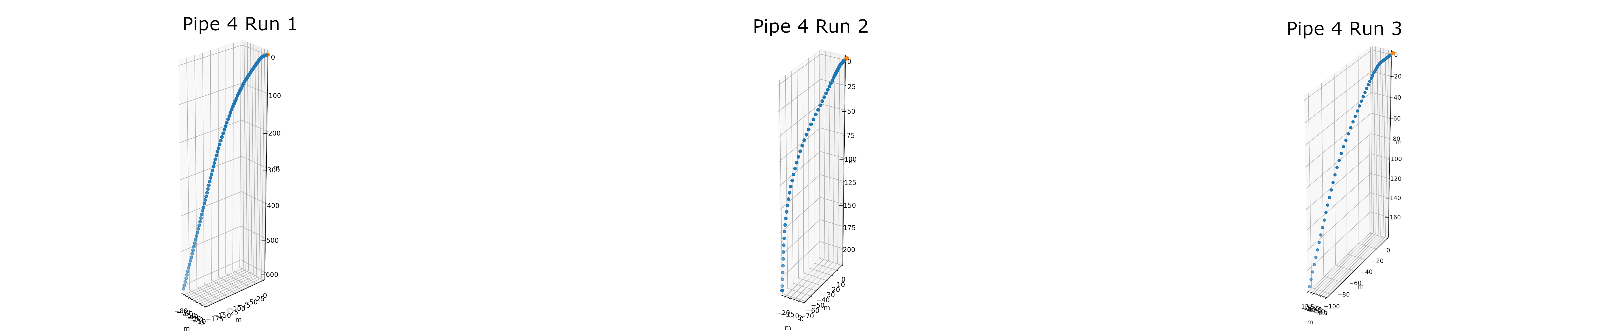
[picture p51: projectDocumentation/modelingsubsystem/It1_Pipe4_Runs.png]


### Experiment Iteration 2

For the second iteration the same data from iteration 1 was used. The first iteration shows a large amount of variablility in the final measurements from endpoints and does not always follow the baseline path shown in the graphs. Our first assumption is to test the gyroscope to see if this is the basis of our errors.

Below are graphs and table entries of Pipe 1 and Pipe 2 with the gyroscope data set to 0.

| Network Number & Run Number | Sample Rate (Hz) | Threshold | Measured vs Baseline Endpoint Difference |
| - | - | - | - |
| 1 - 1 | 26 Hz | 0.1 | (5.80, 2.44, 2.30) meters |
| 1 - 2 | 26 Hz | 0.1 | (5.92, 1.38, 1.16) meters |
| 1 - 3 | 26 Hz | 0.1 | (5.96, 3.09, 2.26) meters |
| 2 - 1 | 26 Hz | 0.1 | (4.28, 2.24, 2.64) meters |
| 2 - 2 | 26 Hz | 0.1 | (6.15, 1.07, 1.70) meters |
| 2 - 3 | 26 Hz | 0.1 | (2.76, 4.54, 4.93) meters |

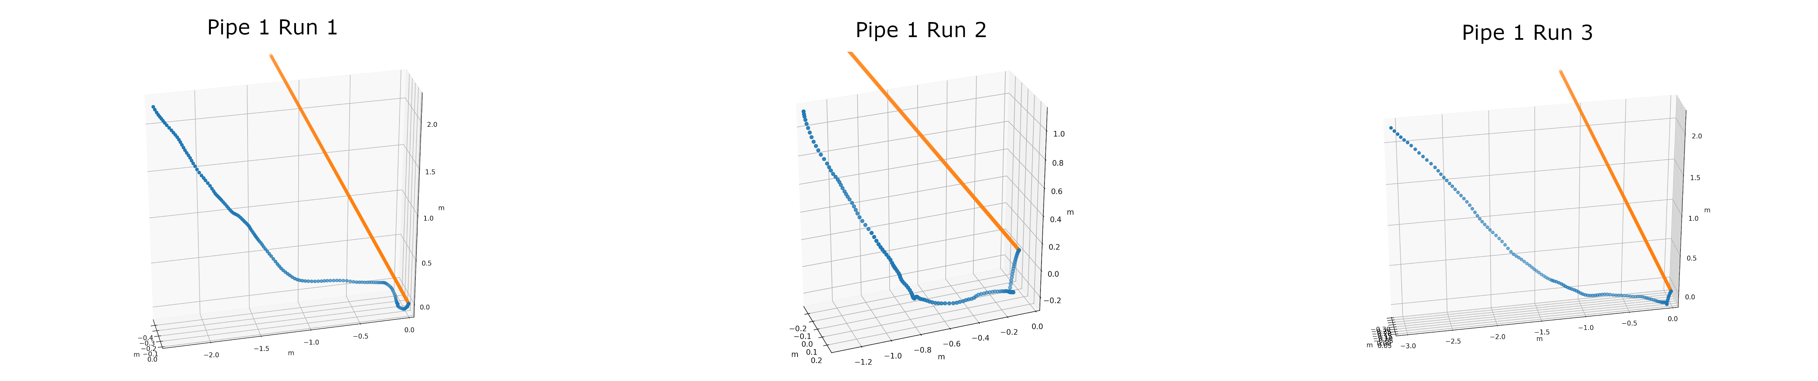
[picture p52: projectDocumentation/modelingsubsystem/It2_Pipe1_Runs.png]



Even though our endpoints are closer, the data does not follow the path of the baseline. This led the team to believe that the gyroscope should not be the issue. However, we are not ruling out the possibility.

### Experiment Iteration 3

For the third iteration the team wanted to test whether the speed and acceleration had anything to do with our skewed results. For this a new set of data was generated with new experimentation. The probe was moved along new and old paths similarly to the methods before, except the speed was increased. Initially, the speed was around 0.8 feet per second. The new speed is around 2.5 - 3 feet per second. These values are estimated from the time and distance covered by the retrieved data, we do not have the means to travel at an exact speed since our system can not be intergrated with the mechanical system.

The first pipe was moved along a straight line 9.144 meters in length. The second pipe was moved along the path of pipe 2 in the initial experiments, 3.35 meters straight and 3 meters to the right. For this iteration the gain value was adjusted to get better results. The gain value controls the strength of the gyroscope based error correction on the system.

| Network Number & Run Number | Sample Rate (Hz) | Threshold | Measured vs Baseline Endpoint Difference |
| - | - | - | - |
| 1 - 1 | 26 Hz | 0.21 | 0.55 | (0.63, 1.60, 1.76) meters |
| 1 - 2 | 26 Hz | 0.21 | 0.55 | (2.63, 1.94, 1.08) meters |
| 1 - 3 | 26 Hz | 0.21 | 0.55 | (2.70, 2.00, 1.10) meters |
| 2 - 1 | 26 Hz | 0.12 | 0.55 | (0.94, 5.38, 2.65) meters |
| 2 - 2 | 26 Hz | 0.2 | 0.55 | (1.73, 1.86, 1.73) meters |
| 2 - 3 | 26 Hz | 0.2 | 0.55 | (3.01, 1.05, 0.217) meters |

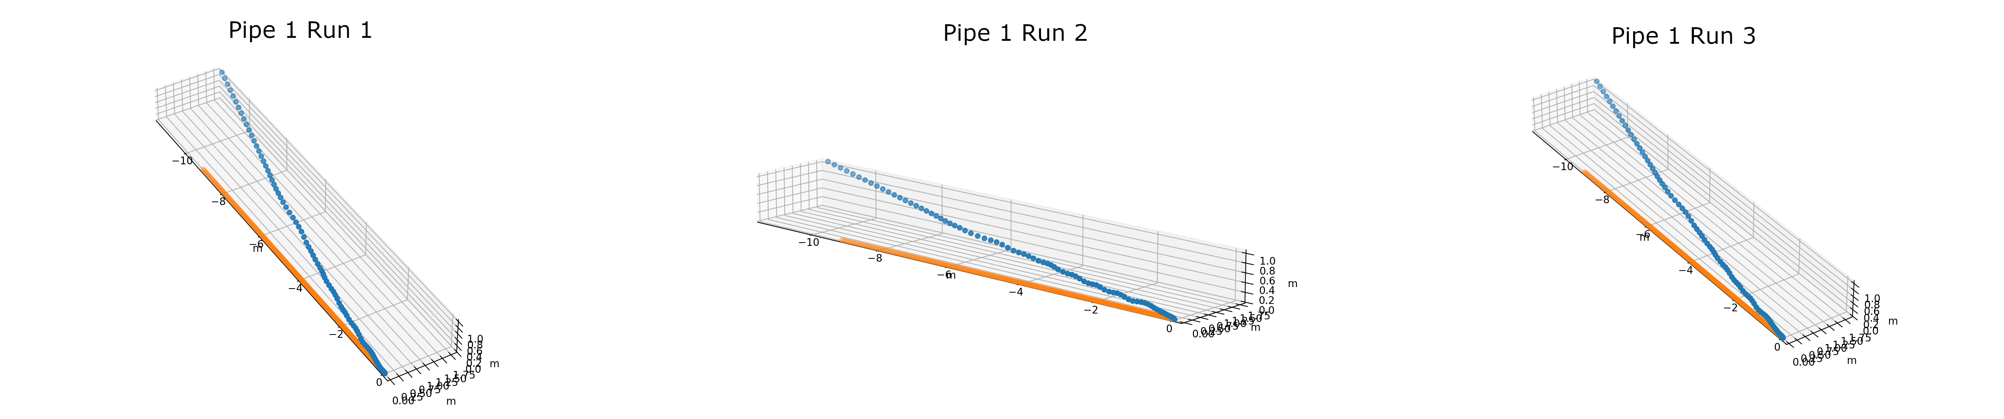
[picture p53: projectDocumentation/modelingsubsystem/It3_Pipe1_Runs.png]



These results look closer to the baseline, however, they are not perfect. This increase in speed has shown to give better data, most likely due to more pronounced data in the IMU. Most experiments using this new iteration turned out similarly to those shown above. The team believes that if the speed was more consistent throughout the experiment the data would be even closer to the baseline.

### Experiment Iteration 4

In the third iteration we increased the speed to obtain better results. Increasing the speed means a faster experiment time, which in turn means less data points in the experiment. Due to this we decided to increase the sampling rate to see if the data would be more defined.

If you increase the sampling rate, you increase the amount of data obtained in the same amount of time. This data then has to be written to the memory for storage. This in turn poses a tradeoff which we had to consider. The faster the sampling rate, the longer the memory would take to write, and the more gaps we would have in the data. The slower the sampling rate, the shorter the memory would take to write, and the more continuous the data would look. Due to this we settled on doubling the sampling rate from 26 Hz to 52 Hz.

| Network Number & Run Number | Sample Rate (Hz) | Threshold | Measured vs Baseline Endpoint Difference |
| - | - | - | - |
| 1 - 1 | 52 Hz | 0.12 | 0.55 | (3.75, 2.92, 0.95) meters |
| 1 - 2 | 52 Hz | 0.21 | 0.35 | (1.00, 2.04, 0.75) meters |
| 1 - 3 | 52 Hz | 0.31 | 0.45 | (2.70, 2.00, 1.10) meters |



These results show that the increased sampling rate helped with more accurate turns. However, it still wasn't fast enough to show any increased accuracy in the measurements. As stated above, changing the sampling rate provides a tradeoff. The team feels as if 52 Hz was the last possible rating for the IMU that would give decently accurate data without adding large holes in the sampling.

### Experiment Iteration 5

The fifth experiment was used to test if the 'free fall' of the IMU would cause errors in the measurements. For this we held the probe 3 feet in the air and dropped it suddenly. Measurements were taken for a short time before and after the fall to measure the baseline of no movement.

| Network Number & Run Number | Sample Rate (Hz) | Threshold | Measured vs Baseline Endpoint Difference |
| - | - | - | - |
| 1 - 1 | 52 Hz | 0.1 | (0.022, 0.55, 0.46) meters |
| 1 - 2 | 52 Hz | 0.25 | (0.009, 0.045, 0.088) meters |

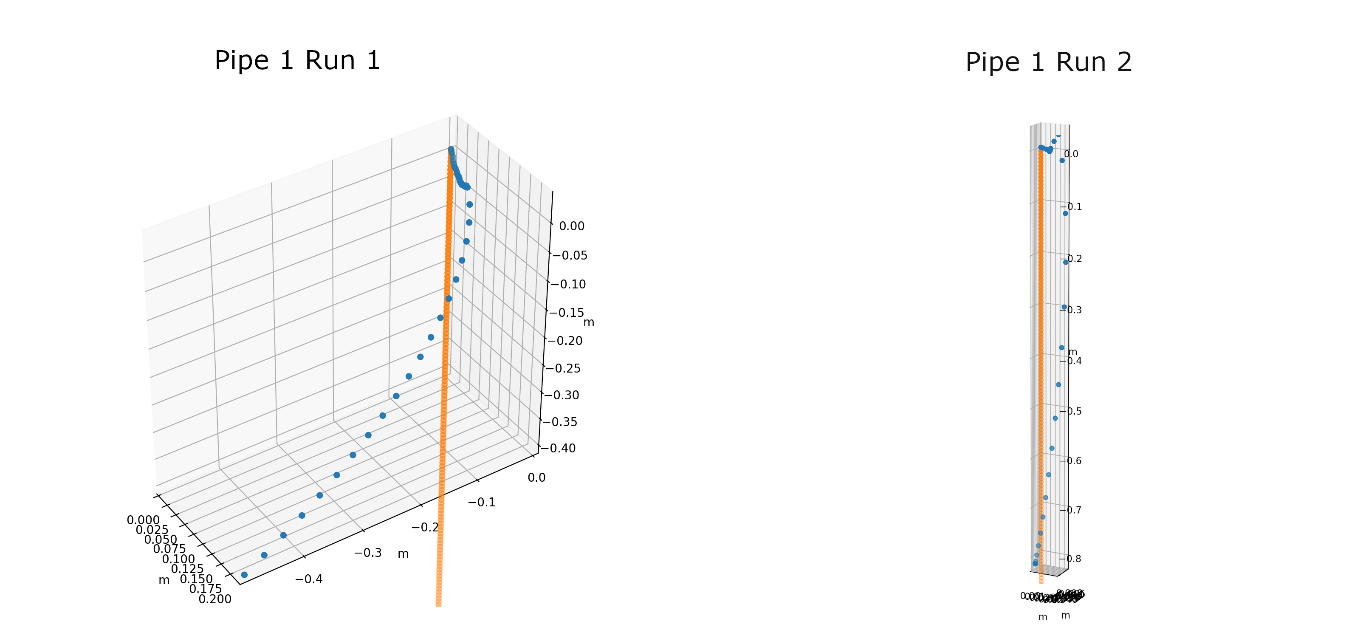
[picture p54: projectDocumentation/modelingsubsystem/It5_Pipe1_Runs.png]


This experiment showed that even though the drop was not always consistent and correct, it shouldn't be causing any large error in our calculations. The errors seen were predicated as the IMU was not expected to always give accurate results in free fall. We had hoped to have more runs and larger heights, however, concern over damaging the probe caused us to end experimentation fairly quickly.

We performed this experiment to test if our previous assumptions of free fall were true and to test the scale of impact. Previous experiments had no reason to be affected by free fall since none of the were dropped uncontrolled. We are now confident that the current system we have employed will handle downward motion adequately and that the chance of free fall will not cause any large errors.

### Experiment Iteration 6

The sixth experiment was used to test the baseline of no movement. This could be used to see if the IMU had any internal errors or if the software was interpreting still movement incorrectly.

| Network Number & Run Number | Sample Rate (Hz) | Threshold | Measured vs Baseline Endpoint Difference |
| - | - | - | - |
| 1 - 1 | 52 Hz | 0.3 | (0.0015, 0.002, 0.0005) meters |
| 1 - 2 | 52 Hz | 0.3 | (0.0015, 0.002, 0.0001) meters |

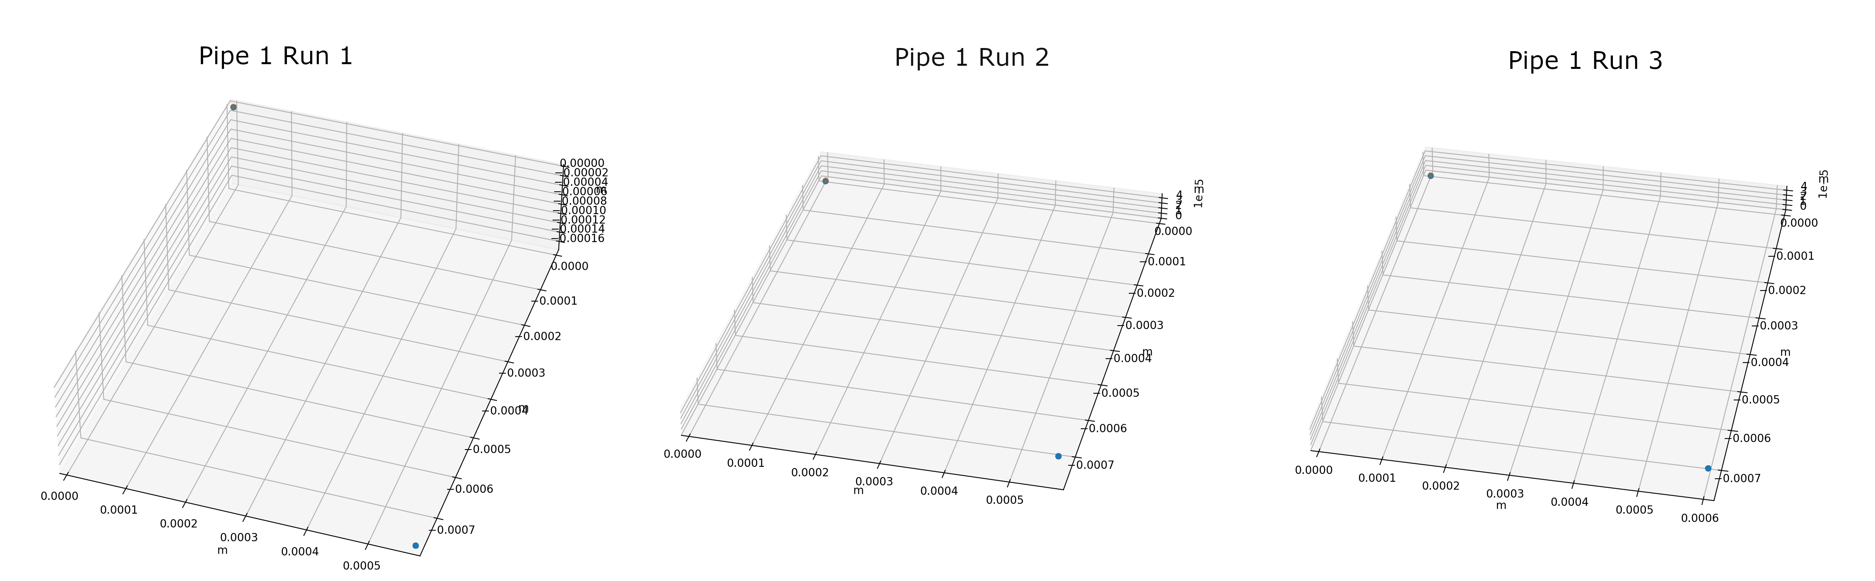
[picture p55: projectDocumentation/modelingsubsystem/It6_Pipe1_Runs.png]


The experiment results show that the still movement gives accurate results and that the error is extremely minimal. It is difficult to see the baseline in the graphs but they are present at (0, 0, 0).

### Experiment Iteration 7

The seventh experiment was used to test if the constant speed of the motors would give better results. The experiment itself had some minor problems that were unavoidable. Firstly, the path was only able to be set up in a short straight line. We were only able to mount the motors to the table so the track could only be the length of the table, 2 meters.

Secondly, the probe had to be put on a box that was then pulled to keep the probe, and the wires safe. The extra friction and caused the probe to move differently than it would have through the pipe in the casing. Also the motor spools needed room to be able to spin so the edge of the table was utilized. This also caused the box to need extra stabilization which caused some tilts in the readings.

The experiment was engineered to be the best it could given the circumstances, but it is not perfect.

| Network Number & Run Number | Sample Rate (Hz) | Threshold | Measured vs Baseline Endpoint Difference |
| - | - | - | - |
| 1 - 1 | 52 Hz | 0.4 | (2.71, 1.45, 1.42) meters |
| 1 - 2 | 52 Hz | 0.4 | (1.99, 0.99, 0.22) meters |

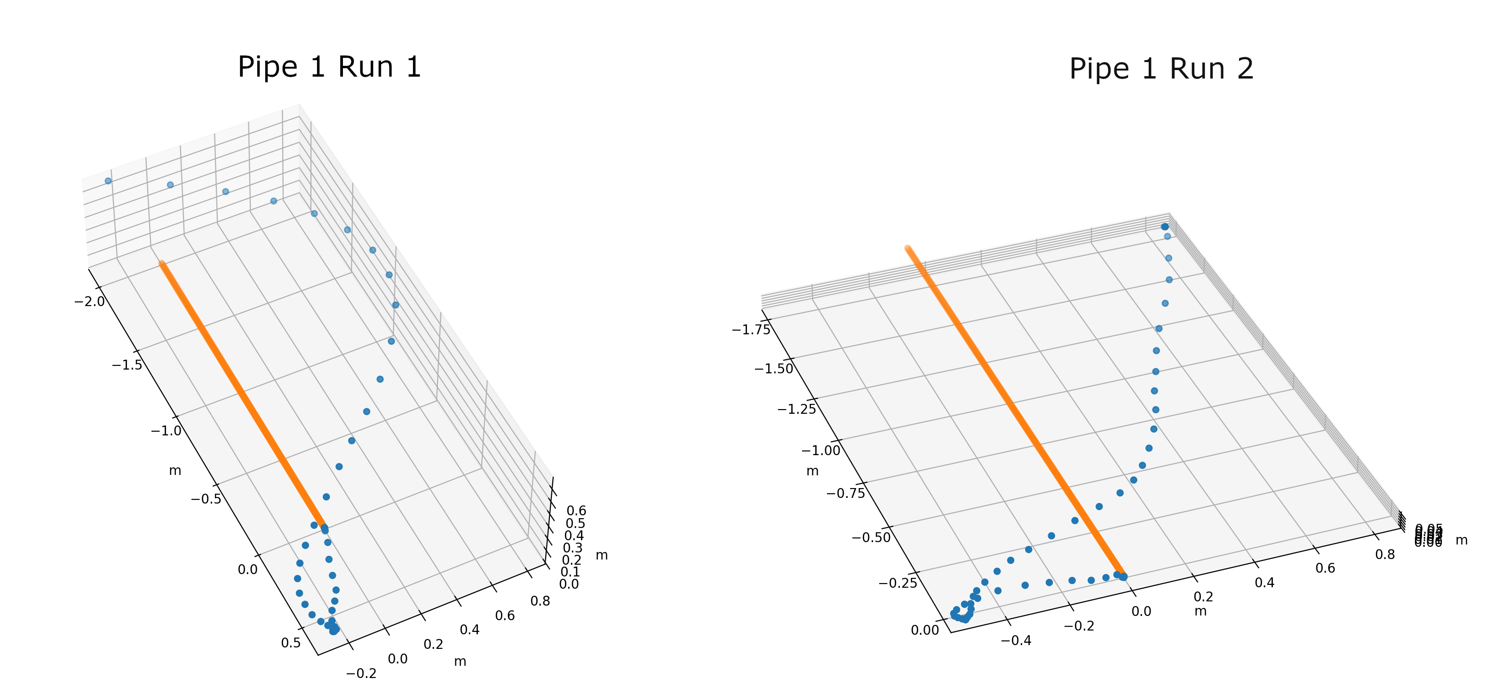
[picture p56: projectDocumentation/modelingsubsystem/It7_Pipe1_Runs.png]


The results were not what the team was expecting but they still seem promising. Due to the experimentation problems the results were predicted to come out with some error. This level of error was not predicted but is explainable. 

Again, the team feels that if the correct hardware and experimentation parameters were met, the results would be much more accurate. 

### Analysis & Recommended Improvements

Our initial experimentation showed large amounts of variability in the final measurements from the endpoints and didn't always follow the baseline path. Error was to be expected initially, but not to this degree. We conducted further experiments to isolate the cause of the error. In these further experiments, the gyroscope was ruled out as a culprit and the speed was brought to light. The later experiments still show error in the recordings but we think we have plausible evidence on what is causing the error.

Firstly, the state of the current drone is causing some of the error, or inability to prevent error, that is difficult to mitigate without redesign. The size and fragility of the current probe keeps it from being tested in its originally designed fashion. The probe cannot fit in the pipe since the wires and extra hardware takes up much more space than would fit inside the pipe. The fragility of the wires also prevents us from testing the system with the mechanical subsystem, as the wires are too delicated to risk such an experiment.

Our second source of error is very similar. Due to the fact that we cannot use the mechanical subsystem in the current design, we cannot move the drone at a consistent speed. Experiment iteration 3 shows that increasing the speed gave better results and the team believes a more constant speed would also help after further investigation into the software. 

We have also come to the conclusion that we need to increase the speed of the probe. This is possible, however, we have selected the current speed to be the least damaging to the probe and the pipe. The redesign would need to ensure that the pipe could endure faster speed than previously calculated and that the new casing would be designed to safely travel at those higher speeds.

The last cause of error, is due to the software using dead reckoning to map the data points. Dead reckoning is at its base an estimation to be able to map a path using the data points, this error will always exist in our program. Dead reckoning uses the position measured and velocity to plot your position.

Dead reckoning (originally called deduced reckoning) will always introduce slight error into the system, one reason is due to the fact that to get the velocity needed for the position calculation, you must integrate the acceleration which adds an unknown C constant. Then to get a position from that velocity it must be integrated again which changes the equation to end in Cx+D where C and D are unknowns. This C and D introduce error, as the number of integrations increases over time to gain the needed positions the error will grow. 

There are two ways to mitigate this error, one is to zero out the error every so often when the software is run and the second is to have a secondary unit such as a GPS, LIDAR, or external sensor to gain the true location so that the error can be calculated out.

Unfortunately, as we are only using data from 6-axis IMUs dead reckoning is the only calculation that was feasible, as our group is only using an accelerometer and gyroscope to gather data. Another fix would be to get a higher quality IMU where it has a secondary unit included. Our code does have error mitigators already added, so to properly lowered the error to near zero we would need to utilize a secondary sensor. 

Our solution was originally planned to mitigate some of these errors. However, as we faced many difficulties during implementation, we had to forego components and methods that were going to assist in reducing this error. Due to this we do not meet our 1" goal for the error range, however, we do have ideas on ways to mitigate this error and design a better system.

Firstly, having the second IMU to check measurements and give better filtering data would be extremely helpful and is already implemented in the redesign. Secondly, having the probe fit inside the casing, and thus the pipe, would hopefully give the sensors a more stable and constant environment to record data in. We could mitigate a lot of sudden movements, accidental offsets, and we could keep the speed much more constant. Finally, having secondary systems, like a GPS or magnetometer, would help tremendously since IMUs have difficulty measuring the incline/decline in a path and are sensitive to sudden changes in motion.

Even though the team was not able to get the data within the margins of success, we believe we have determined the cause of the error and have hypothesised on possible fixes to this error. We have taken individual tests of all the subsystems, software, and hardware pieces. The memory is tested in Experiment 3 and shows perfect execution. The software has been tested with example data and shows to be a promising asset. Finally, the IMU is tested in this experiment, however, it is difficult to break down the system any further than we already have. 

We believe that the best way to fix the error in our system would be to move forward with the redesign and conduct the original experiments in the way they were first imagined, with one small change. We would like to run the experiments with varying speeds to truly test what constant speed would give the best results before the sampling rate would need to be increased.

## Experiment 3
The third experiment was designed to test the capabilities of the memory subsystem. We used this experiment to validate that the memory would be able to hold up to 5000 feet or 20 minutes worth of data, and to keep the data when the device was powered off and on. The experiment consisted of running the device for various time lengths, measuring the amount of data that was stored in the memory, verifying that the memory had not overflowed, and verifying that the data was still intact and unmodified.

We were able to use the timestamp provided by the IMU to measure the exact amount of time data was measured. The IMU was running at 26 Hz and polled both the accelerometer, gyroscope, and timestamp. Each data entry consisted of 7 bytes, 1 tag byte and 6 data bytes. Since the data rate and size were constant the data looks exactly as predicted.

| Run Time | Bytes Stored | Bytes Retrieved | Calculated Bytes Remaining In Memory |
| --- | --- | --- | --- |
| 1 minute  | 32,760 bytes | 32,760 bytes | 16,744,456 bytes |
| 5 minutes | 163,800 bytes| 163,800 bytes | 16,613,416 bytes |
| 10 minutes| 327,600 bytes| 327,600 bytes | 16,449,616 bytes |
| 15 minutes| 491,400 bytes| 491,400 bytes | 16,285,816 bytes |
| 20 minutes| 655,200 bytes| 655,200 bytes | 16,122,016 bytes |

### Analysis & Recommended Improvements
The memory subsystem was easily able to collect data continuously for 20 minutes which is well above what it should ever actually have to collect in a real application. Recommended improvements are purely to increase the performance of the system and convenience of the programmer. The only improvement that the team could find was to change the memory to be able to be written to without being erased. The current memory has to be erased everytime you want to change the data in a byte so this caused a bit of a performance hit on the system. It was not enough to change the data but if we sampled at a higher frequency, it would have caused a problem.

## Experiment 4
The fourth experiment focused on verifying that the device's battery life was within the specification defined within previous documents. This specification stated that the batteries must last long enough for the probe to collect 20 minutes worth of data at minimum. For this experiment, the device was powered only via the series connection of 3 AA batteries connected to the Vin and GND pins of the Arduino Nano. Load current was measured using a DMM, and then the initial battery voltage was measured. After recording the initial battery voltage, the device was allowed to continuously poll data for 20 minutes uninterrupted. After the 20 minutes were up, the battery voltage was measured again. This test was performed 3 times. The data is shown in the table below. 

| Run # | Run Time | Initial Battery Voltage (V) | Post-test Battery Voltage (V) | Load Current (mA)|
| ----- | --- | --- | --- | --- |
| 1 | 20 minutes | 5.08 | 5.03 | 15-18 |
| 2 | 20 minutes | 5.03 | 4.98 | 15-18 |
| 3 | 20 minutes | 4.98 | 4.92 | 15-18 |

 Given the initial specification of 20 minutes minimum run time, this experiment verifies that the device comfortably meets our requirements. It should be noted that due to the dropout voltage of the 3.3V LDO, the device will only remain powered until the total battery voltage reaches around 3.67V (as calculated in the Power Subsystem Signoff). However, even though the device will only be functional until the battery voltage approaches this threshold, it is clear that the device exceeds our minimum run time requirement. Given the load current in the table above, and the manufacturer discharge curve for the batteries used in this experiment (Duracell Coppertop AA's), we can estimate the battery life of the device to be around 50-100 hours when using these batteries.

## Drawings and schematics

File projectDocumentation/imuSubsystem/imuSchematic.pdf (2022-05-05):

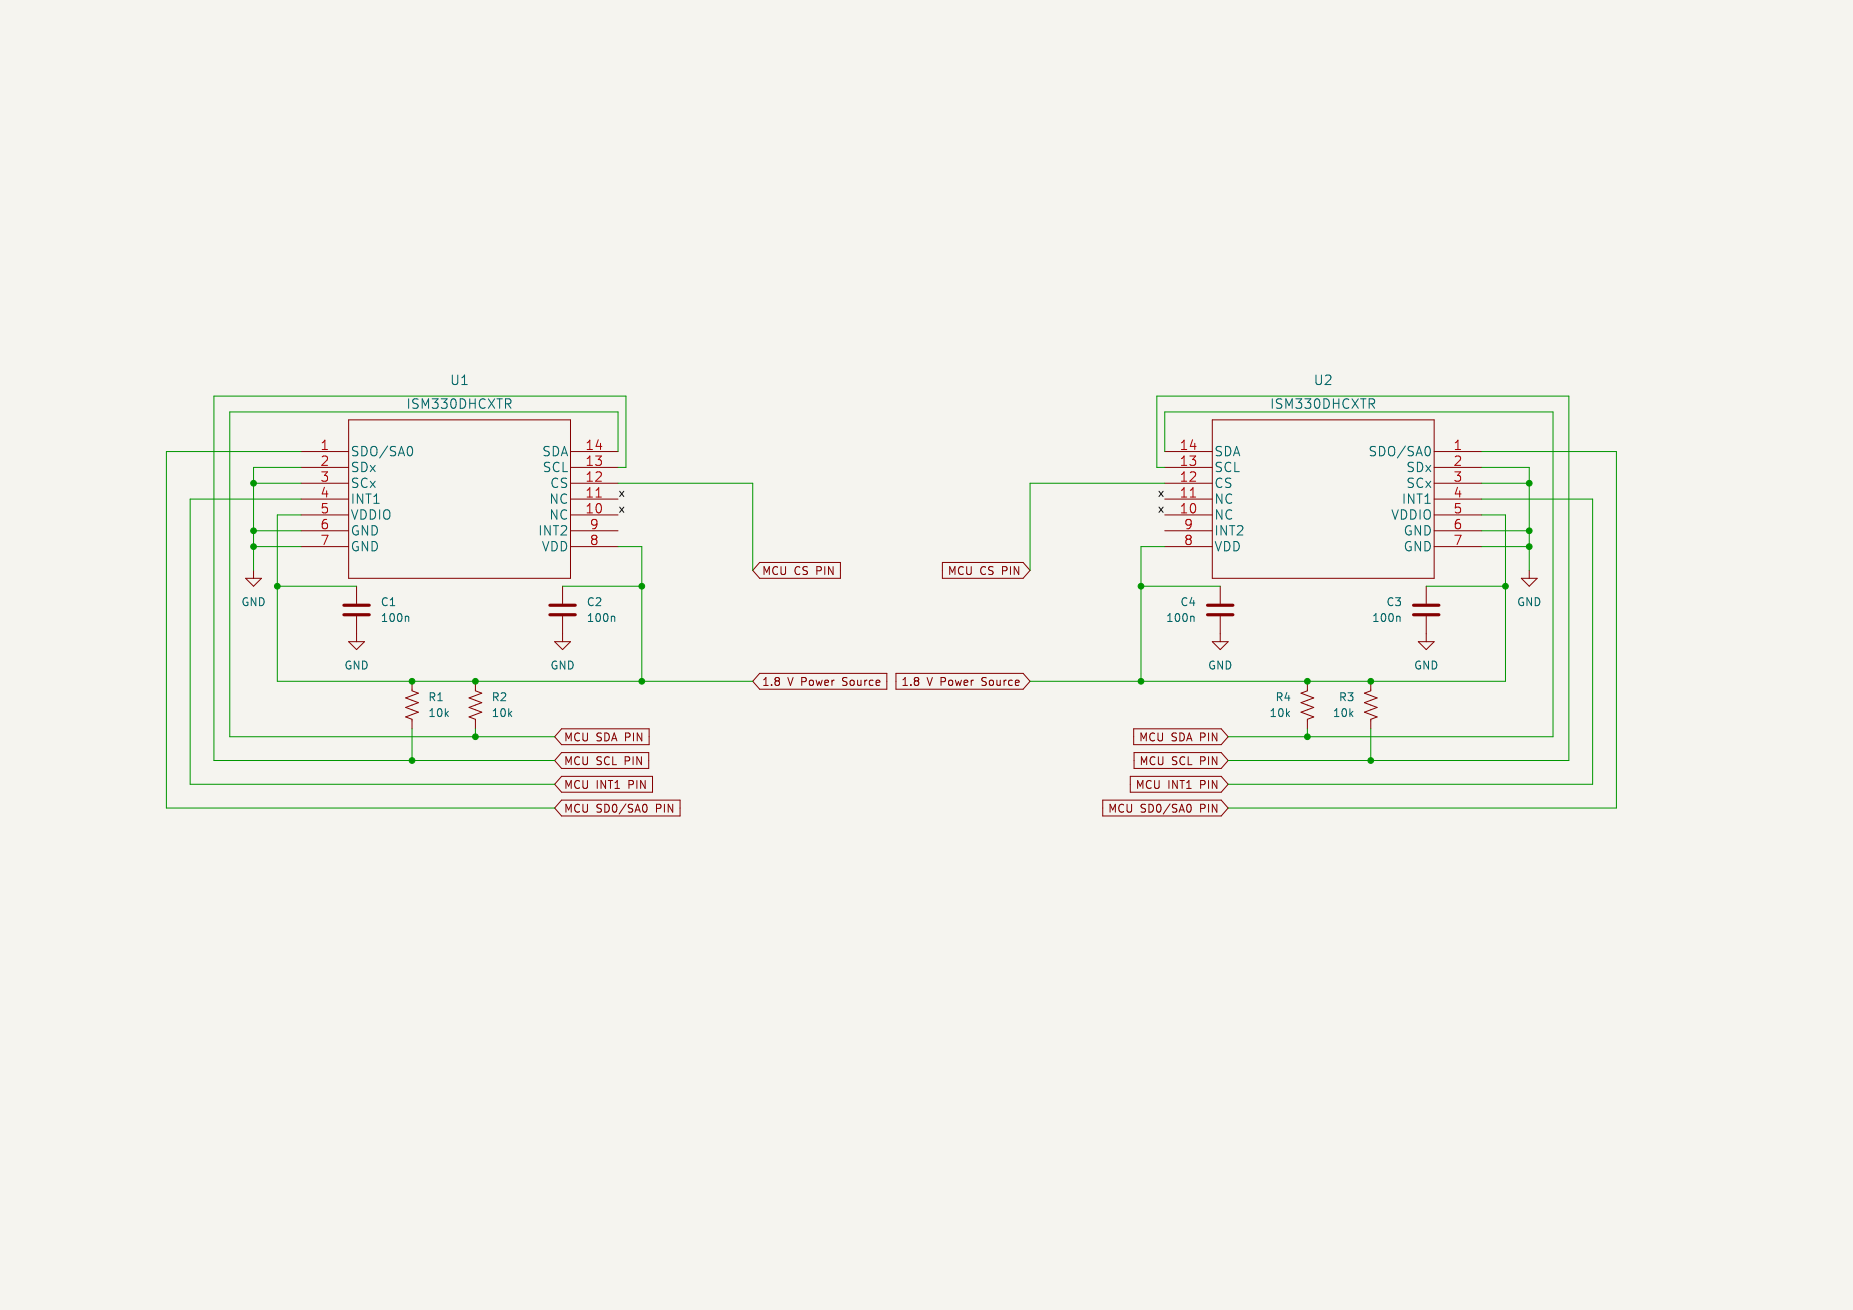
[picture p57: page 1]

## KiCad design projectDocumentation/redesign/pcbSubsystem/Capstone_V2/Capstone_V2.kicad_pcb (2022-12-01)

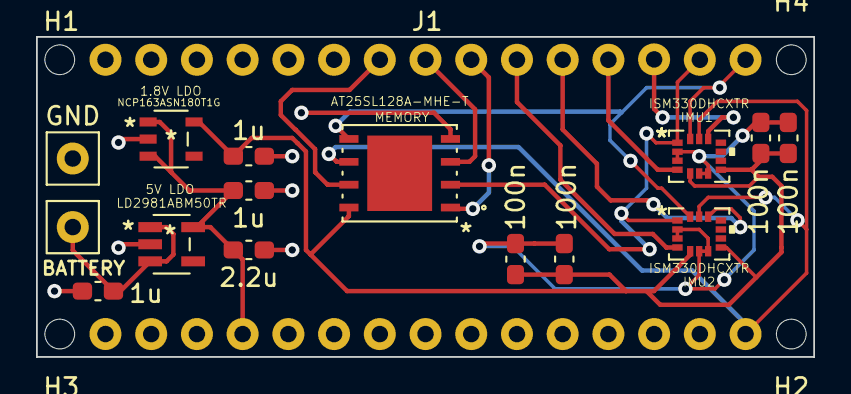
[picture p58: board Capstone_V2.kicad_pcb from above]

Board: 2 copper layers, 43.2 x 17.8 mm, 21 parts (0 on the bottom side), 15 nets.

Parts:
1.8V LDO: NCP163ASN180T1G
1u, 1u#2, 1u#3: 1u; C_0603_1608Metric_Pad1.08x0.95mm_HandSolder
2.2u: 2.2u; C_0603_1608Metric_Pad1.08x0.95mm_HandSolder
5V LDO: LD2981ABM50TR
100n, 100n#2, 100n#3, 100n#4: 100n; C_0603_1608Metric_Pad1.08x0.95mm_HandSolder
BATTERY: TestPoint; TestPoint_THTPad_2.5x2.5mm_Drill1.2mm
GND: TestPoint; TestPoint_THTPad_2.5x2.5mm_Drill1.2mm
H1, H2, H3, H4: MountingHole; MountingHole_2.1mm
IMU1, IMU2: ISM330DHCXTR
J1, J2: Conn_01x15; Molex_KK-254_AE-6410-15A_1x15_P2.54mm_Vertical
MEMORY: AT25SL128A-MHE-T

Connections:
1.8 V: 1.8V LDO.5 (OUT), 1u.1, 100n.2, 100n#2.2, 100n#3.2, 100n#4.2, IMU1.5 (VDDIO), IMU1.8 (VDD), IMU2.5 (VDDIO), IMU2.8 (VDD), MEMORY.8 (VCC)
5 V IN: 1.8V LDO.1 (IN), 1.8V LDO.3 (EN), 1u#2.1, 2.2u.1, 5V LDO.5 (VOUT), J2.12
/RST: J1.3, J2.13
Battery: 1u#3.1, 5V LDO.1 (VIN), 5V LDO.3 (INHIBIT), BATTERY.1
GND: 1.8V LDO.2 (GND), 1u.2, 1u#2.2, 1u#3.2, 2.2u.2, 5V LDO.2 (GND), 100n.1, 100n#2.1, 100n#3.1, 100n#4.1, GND.1, IMU1.2 (SDx), IMU1.3 (SCx), IMU1.6 (GND), IMU1.7 (GND), IMU2.2 (SDx), IMU2.3 (SCx), IMU2.6 (GND), IMU2.7 (GND), J1.4, J2.14, MEMORY.4 (GND)
HOLD PIN: J1.7, MEMORY.7 (*HOLDIO3)
IMU1 CS PIN: IMU1.12 (CS), J1.13
IMU1 INT1 PIN: IMU1.4 (INT1), J1.12
IMU2 CS PIN: IMU2.12 (CS), J1.11
IMU2 INT1 PIN: IMU2.4 (INT1), J1.10
MEM CS PIN: J1.9, MEMORY.1 (*CS)
SPI CLK: IMU1.13 (SCL), IMU2.13 (SCL), J2.1, MEMORY.6 (SCK)
SPI MISO: IMU1.14 (SDA), IMU2.14 (SDA), J1.15, MEMORY.5 (SIIO0)
SPI MOSI: IMU1.1 (SDO/SA0), IMU2.1 (SDO/SA0), J1.14, MEMORY.2 (SOIO1)
WP PIN: J1.8, MEMORY.3 (*WPIO2)

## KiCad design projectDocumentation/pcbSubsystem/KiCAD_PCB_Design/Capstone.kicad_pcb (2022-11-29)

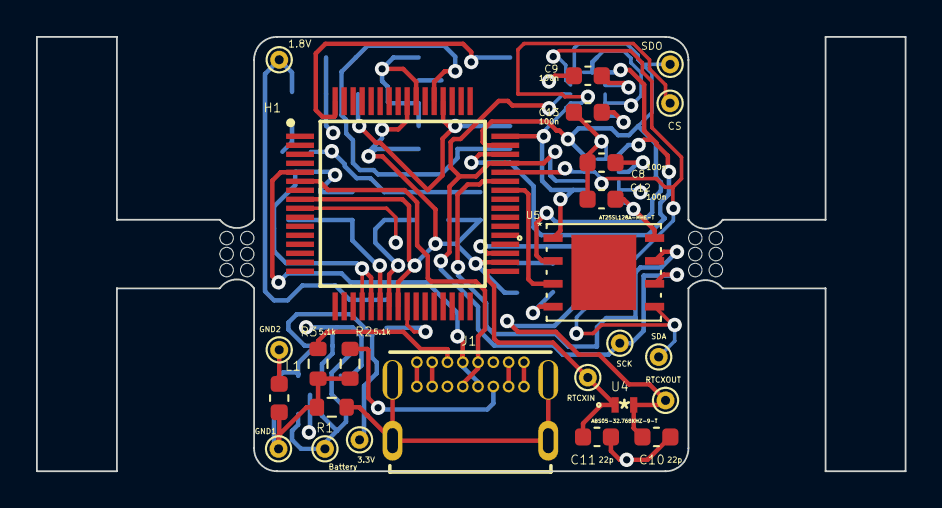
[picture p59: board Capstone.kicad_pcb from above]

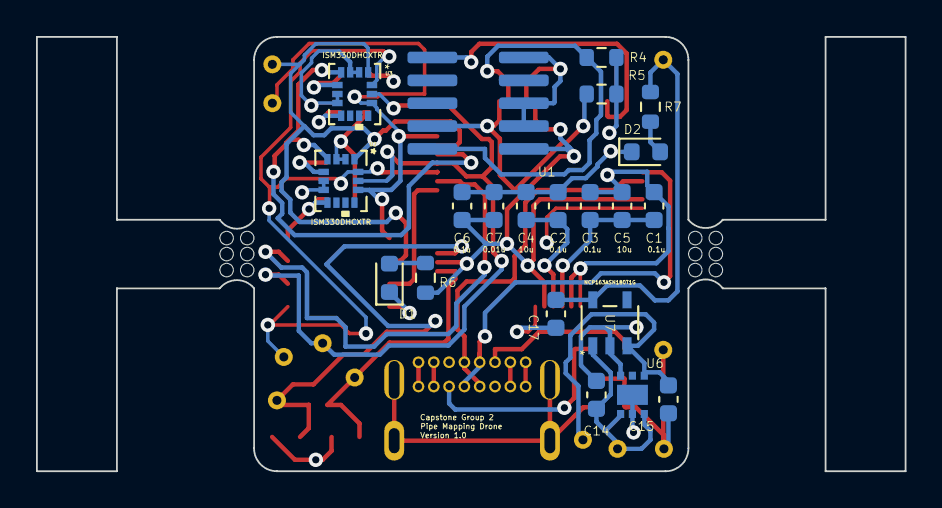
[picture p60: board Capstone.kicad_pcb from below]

Board: 4 copper layers, 48.3 x 24.1 mm, 50 parts (21 on the bottom side), 25 nets.

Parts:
1.8V, 3.3V: TestPoint; TestPoint_THTPad_D1.0mm_Drill0.5mm
 : MountingHole_2.1mm
 #2,  #3,  #4: MountingHole_2.1mm
Battery: TestPoint; TestPoint_THTPad_D1.0mm_Drill0.5mm
C1, C2, C3, C6: 0.1u; C_0603_1608Metric
C4, C5: 10u; C_0603_1608Metric
C7: 0.01u; C_0603_1608Metric
C8, C9, C12, C13: 100n; C_0603_1608Metric
C10, C11: 22p; C_0603_1608Metric
C14, C15, C17: 1u; C_0603_1608Metric
CS: TestPoint; TestPoint_THTPad_D1.0mm_Drill0.5mm
D1, D2: LED; LED_0603_1608Metric
GND1, GND2: TestPoint; TestPoint_THTPad_D1.0mm_Drill0.5mm
H1: LPC54113J128BD64QL; QFP50P1200X1200X160-64N
J1: USB4085-GF-A_REVA4; GCT_USB4085-GF-A_REVA4
L1: L; L_0603_1608Metric
R1, R6, R7: 1M; R_0603_1608Metric
R2, R3: 5.1k; R_0603_1608Metric
R4, R5: 10k; R_0603_1608Metric
RTCXIN: TestPoint; TestPoint_THTPad_D1.0mm_Drill0.5mm
RTCXOUT: TestPoint; TestPoint_THTPad_D1.0mm_Drill0.5mm
SCK: TestPoint; TestPoint_THTPad_D1.0mm_Drill0.5mm
SDA: TestPoint; TestPoint_THTPad_D1.0mm_Drill0.5mm
SDO: TestPoint; TestPoint_THTPad_D1.0mm_Drill0.5mm
U1: SWD_485-4048
U2, U3: ISM330DHCXTR
U4: ABS05-32.768KHZ-9-T
U5: AT25SL128A-MHE-T
U6: NCP730BMT330TBG
U7: NCP163ASN180T1G

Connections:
1.8V: 1.8V.1, C8.1, C9.1, C12.1, C13.1, C17.1, R7.1, U2.5 (VDDIO), U2.8 (VDD), U3.5 (VDDIO), U3.8 (VDD), U5.8 (VCC), U7.5 (OUT)
3.3V: 3.3V.1, C1.2, C2.1, C3.2, C4.1, C5.1, C6.1, C7.1, C15.1, H1.8 (VDD_1), H1.22 (VREFP), H1.23 (VDDA), H1.24 (VDD_2), H1.34 (VDD_3), H1.56 (VDD_4), R4.1, R5.1, R6.1, U1.1 (VCC), U6.1 (OUT), U7.3 (EN)
Battery: Battery.1, C14.1, U6.4 (EN), U6.6 (IN), U7.1 (IN)
GND1: C2.2, C4.2, C6.2, C7.2, C8.2, C9.2, C10.2, C11.2, C12.2, C13.2, C14.2, C15.2, C17.2, D1.1 (K), D2.1 (K), GND1.1, H1.9 (VSS_1), H1.25 (VSS_2), H1.55 (VSS_3), J1.A1 (GND), J1.A12 (GND), J1.B1 (GND), J1.B12 (GND), L1.1, R1.2, R2.2, R3.2, U1.3 (GND), U1.5 (GND), U1.9 (GND), U2.2 (SDx), U2.3 (SCx), U2.6 (GND), U2.7 (GND), U3.2 (SDx), U3.3 (SCx), U3.6 (GND), U3.7 (GND), U5.4 (GND), U6.3 (GND), U6.5 (NC/PG), U6.7 (EP), U7.2 (GND)
GND2: C1.1, C3.1, C5.2, GND2.1, H1.20 (VSSA), H1.21 (VREFN), L1.2
unnamed: C10.1, H1.35 (RTCXOUT), RTCXOUT.1, U4.2
unnamed: C11.1, H1.33 (RTCXIN), RTCXIN.1, U4.1
unnamed: D1.2 (A), R6.2
unnamed: D2.2 (A), R7.2
unnamed: H1.5 (USB_DP), J1.A6 (DP1), J1.B6 (DP2)
unnamed: H1.6 (USB_DM), J1.A7 (DN1), J1.B7 (DN2)
unnamed: H1.42 (PIO1_11), U5.3 (*WPIO2)
unnamed: H1.43 (PIO0_8), U5.7 (*HOLDIO3)
unnamed: H1.44 (PIO0_9), SDA.1, U2.14 (SDA), U3.14 (SDA), U5.5 (SIIO0)
unnamed: H1.45 (PIO0_10), SCK.1, U2.13 (SCL), U3.13 (SCL), U5.6 (SCK)
unnamed: H1.46 (PIO0_11), U2.4 (INT1), U3.4 (INT1)
unnamed: H1.47 (PIO0_12), SDO.1, U2.1 (SDO/SA0), U3.1 (SDO/SA0), U5.2 (SOIO1)
unnamed: CS.1, H1.48 (PIO0_13), U2.12 (CS), U3.12 (CS), U5.1 (*CS)
unnamed: H1.52 (SWCLK/PIO0_16), R5.2, U1.4 (SWDCLK)
unnamed: H1.53 (SWDIO/PIO0_17), R4.2, U1.2 (SWDIO)
unnamed: H1.64 (RESET), U1.10 (RESET)
unnamed: J1.A4 (VBUS), J1.A9 (VBUS), J1.B4 (VBUS), J1.B9 (VBUS)
unnamed: J1.A5 (CC1), R3.1
unnamed: J1.B5 (CC2), R2.1
unnamed: J1.P1 (SHELL), J1.P2 (SHELL), J1.P3 (SHELL), J1.P4 (SHELL), R1.1

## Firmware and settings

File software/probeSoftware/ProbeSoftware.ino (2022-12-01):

#include <SoftwareSerial.h>
#include <SPI.h>

// Defined all the pins needed
#define RX_PIN 30
#define TX_PIN 31

#define IMU_INT_PIN 2
#define IMU_CS_PIN 3

#define MEM_CS_PIN 4
#define MEM_HOLD_PIN 6
#define MEM_WP_PIN 5

#define SPI_SCK_PIN 13
#define SPI_MOSI_PIN 11
#define SPI_MISO_PIN 12

#define SWITCH_PIN 9
#define D8_PIN 8
#define D7_PIN 7

// Function definitions
void initSPI();
void writeCommand(int cs, uint8_t command);
void writeByte(int cs, uint16_t data);
uint8_t readByte(int cs, uint8_t addr);

// Define states
bool pcConnected = false;

// Define variables
uint8_t fifoData[140 * 7];
uint16_t numEntries;

uint32_t address = 0x00000000;
uint32_t addressTemp = 0;

void setup() {
  delay(20);

  Serial.begin(57600);

  // Initialize the pins
  pinMode(IMU_INT_PIN, INPUT);
  pinMode(IMU_CS_PIN, OUTPUT);
  digitalWrite(IMU_CS_PIN, HIGH);
  pinMode(MEM_CS_PIN, OUTPUT);
  digitalWrite(MEM_CS_PIN, HIGH);
  pinMode(MEM_HOLD_PIN, OUTPUT);
  digitalWrite(MEM_HOLD_PIN, HIGH);
  pinMode(MEM_WP_PIN, OUTPUT);
  digitalWrite(MEM_WP_PIN, HIGH);
  pinMode(SWITCH_PIN, INPUT);
  pinMode(D8_PIN, OUTPUT);
  digitalWrite(D8_PIN, HIGH);
  pinMode(D7_PIN, OUTPUT);
  digitalWrite(D7_PIN, LOW);

  initSPI();

  // Initialize the IMU
  // Set the gyro and accel to write to FIFO at 52 Hz
  writeByte(IMU_CS_PIN, 0x0933);
  
  // Configure INT1 to trigger on FIFO full and COUNTER_BDR_IA
  writeByte(IMU_CS_PIN, 0x0D60);

  // Configure the batch counter to toggle at 128
  writeByte(IMU_CS_PIN, 0x0B00);
  writeByte(IMU_CS_PIN, 0x0C40);

  // Configure the gyro and accel to poll at 52 Hz
  writeByte(IMU_CS_PIN, 0x1030);
  writeByte(IMU_CS_PIN, 0x1130);

  // Enable the timestamp counter
  writeByte(IMU_CS_PIN, 0x1920);

  if (digitalRead(SWITCH_PIN) == HIGH) {
    pcConnected = true;
  } else {
    pcConnected = false;

    int status = readByte(MEM_CS_PIN, 0x05);
    while (status & 0x01) {
      status = readByte(MEM_CS_PIN, 0x05);
    }

    // Erase the memory
    writeCommand(MEM_CS_PIN, 0x06);

    status = readByte(MEM_CS_PIN, 0x05);
    while (!(status & 0x02)) {
      status = readByte(MEM_CS_PIN, 0x05);
    }

    digitalWrite(MEM_CS_PIN, LOW);
    SPI.transfer(0x52);
    SPI.transfer(0x00);
    SPI.transfer(0x00);
    SPI.transfer(0x00);
    digitalWrite(MEM_CS_PIN, HIGH);

    status = readByte(MEM_CS_PIN, 0x05);
    while (status & 0x01) {
      status = readByte(MEM_CS_PIN, 0x05);
    }

    delay(2000);
  }

  // Set the FIFO to FIFO mode
  writeByte(IMU_CS_PIN, 0x0A80);  // Reset the FIFO first
  writeByte(IMU_CS_PIN, 0x0A81);

  address = 0x00000000;
}

void loop() {
  if (!pcConnected) {
    while (1) {
      // Check the interrupt pin
      if (digitalRead(IMU_INT_PIN) == HIGH) {
        // Get the number of entries in the FIFO
        uint8_t fifoEntries;
        fifoEntries = readByte(IMU_CS_PIN, 0xBA);

        // Serial.println(fifoEntries);

        int j = 0;
        for (int i = 0; i < fifoEntries; ++i) {
          fifoData[j++] = readByte(IMU_CS_PIN, 0xF8); // Tag byte
          fifoData[j++] = readByte(IMU_CS_PIN, 0xFA); // Upper x byte
          fifoData[j++] = readByte(IMU_CS_PIN, 0xF9); // Lower x byte
          fifoData[j++] = readByte(IMU_CS_PIN, 0xFC); // Upper y byte
          fifoData[j++] = readByte(IMU_CS_PIN, 0xFB); // Lower y byte
          fifoData[j++] = readByte(IMU_CS_PIN, 0xFE); // Upper z byte
          fifoData[j++] = readByte(IMU_CS_PIN, 0xFD); // Lower z byte
        }

        ++numEntries;

        // DEBUG INFO - Prints the IMU information
        // j = 0;
        // for (int i = 0; i < 136; i++) {
        //   uint8_t t = fifoData[j++];
        //   int16_t d;
        //   if ((t & 0xF8) == 16) {
        //     // Serial.print("  ");
        //     Serial.print(t, DEC);
        //     Serial.print("  ");
        //     d = (fifoData[j++] << 8) | fifoData[j++];
        //     Serial.print((d * 0.061 * 9.80665 / 1000) * 0.101971621, DEC);
        //     Serial.print("  ");
        //     d = (fifoData[j++] << 8) | fifoData[j++];
        //     Serial.print((d * 0.061 * 9.80665 / 1000) * 0.101971621, DEC);
        //     Serial.print("  ");
        //     d = (fifoData[j++] << 8) | fifoData[j++];
        //     Serial.print((d * 0.061 * 9.80665 / 1000) * 0.101971621, DEC);
        //     // Serial.print(" g");
        //     Serial.print("\r\n   ");
        //   } else if ((t & 0xF8) == 32) {
        //     uint32_t time = 0;
        //     Serial.print(t, DEC);
        //     Serial.print("  ");
        //     time = ((fifoData[j + 2] << 24) | (fifoData[j + 3] << 16) | (fifoData[j] << 8) | fifoData[j + 1]);
        //     j += 6;
        //     Serial.print(time, DEC);
        //     Serial.print("\r\n   ");
        //     // Serial.print(" us\r\n");
        //   } else if((t & 0xF8) == 8) {
        //     Serial.print(t, DEC);
        //     Serial.print("  ");
        //     d = (fifoData[j++] << 8) | fifoData[j++];
        //     Serial.print((d * 0.017453293 * 8.75 / 1000) * 57.2958, DEC);
        //     Serial.print("  ");
        //     d = (fifoData[j++] << 8) | fifoData[j++];
        //     Serial.print((d * 0.017453293 * 8.75 / 1000) * 57.2958, DEC);
        //     Serial.print("  ");
        //     d = (fifoData[j++] << 8) | fifoData[j++];
        //     Serial.print((d * 0.017453293 * 8.75 / 1000) * 57.2958, DEC);
        //     // Serial.print(" deg/s");
        //     Serial.print("\r\n   ");
        //   } else {
        //     Serial.println(fifoData[j]);
        //     j += 6;
        //   }
        // }

        // Reset the FIFO buffer
        writeByte(IMU_CS_PIN, 0x0A80);
        writeByte(IMU_CS_PIN, 0x0A81);

        // Set the write enable latch
        writeCommand(MEM_CS_PIN, 0x06);

        // Write the data to memory
        digitalWrite(MEM_CS_PIN, LOW);
        SPI.transfer(0x02);
        SPI.transfer(0x00);
        SPI.transfer(0x00);
        SPI.transfer(0x00);
        SPI.transfer16(numEntries);
        digitalWrite(MEM_CS_PIN, HIGH);

        // Check that the memory isn't busy everytime before writing
        int status = 0;
        status = readByte(MEM_CS_PIN, 0x05);
        while (status & 0x01) {
          status = readByte(MEM_CS_PIN, 0x05);
        }

        // Set the write enable latch
        writeCommand(MEM_CS_PIN, 0x06);

        address += 0x100;
        addressTemp = address >> 16;
        // Write to the first block of memory
        digitalWrite(MEM_CS_PIN, LOW);
        SPI.transfer(0x02);
        SPI.transfer((uint8_t)addressTemp);
        addressTemp = address >> 8;
        SPI.transfer((uint8_t)addressTemp);
        addressTemp = address;
        SPI.transfer((uint8_t)addressTemp);

        // OLD CODE CHANGED TO LINE BELOW
        // for (int i = 0; i < 256; ++i) {
        //   SPI.transfer(fifoData[i]);
        // }

        SPI.transfer(&fifoData[0], 256);

        digitalWrite(MEM_CS_PIN, HIGH);

        delay(5);

        status = readByte(MEM_CS_PIN, 0x05);
        while (status & 0x01) {
          status = readByte(MEM_CS_PIN, 0x05);
        }

        // Set the write enable latch
        writeCommand(MEM_CS_PIN, 0x06);

        address += 0x100;
        addressTemp = address >> 16;
        // Write to the second block of memory
        digitalWrite(MEM_CS_PIN, LOW);
        SPI.transfer(0x02);
        SPI.transfer((uint8_t)addressTemp);
        addressTemp = address >> 8;
        SPI.transfer((uint8_t)addressTemp);
        addressTemp = address;
        SPI.transfer((uint8_t)addressTemp);

        // for (int i = 0; i < 256; ++i) {
        //   SPI.transfer(fifoData[i + 256]);
        // }

        SPI.transfer(&fifoData[256], 256);

        digitalWrite(MEM_CS_PIN, HIGH);

        delay(5);

        status = readByte(MEM_CS_PIN, 0x05);
        while (status & 0x01) {
          status = readByte(MEM_CS_PIN, 0x05);
        }

        // Set the write enable latch
        writeCommand(MEM_CS_PIN, 0x06);

        address += 0x100;
        addressTemp = address >> 16;
        // Write to the third free block for the next entry block
        digitalWrite(MEM_CS_PIN, LOW);
        SPI.transfer(0x02);
        SPI.transfer((uint8_t)addressTemp);
        addressTemp = address >> 8;
        SPI.transfer((uint8_t)addressTemp);
        addressTemp = address;
        SPI.transfer((uint8_t)addressTemp);

        // for (int i = 0; i < 256; ++i) {
        //   SPI.transfer(fifoData[i + 512]);
        // }

        SPI.transfer(&fifoData[512], 256);

        digitalWrite(MEM_CS_PIN, HIGH);

        delay(5);

        status = readByte(MEM_CS_PIN, 0x05);
        while (status & 0x01) {
          status = readByte(MEM_CS_PIN, 0x05);
        }

        // Set the write enable latch
        writeCommand(MEM_CS_PIN, 0x06);

        address += 0x100;
        addressTemp = address >> 16;
        // Write to the third.5 free block for the next entry block
        digitalWrite(MEM_CS_PIN, LOW);
        SPI.transfer(0x02);
        SPI.transfer((uint8_t)addressTemp);
        addressTemp = address >> 8;
        SPI.transfer((uint8_t)addressTemp);
        addressTemp = address;
        SPI.transfer((uint8_t)addressTemp);

        // for (int i = 0; i < 184; ++i) {
        //   SPI.transfer(fifoData[i + 768]);
        // }

        SPI.transfer(&fifoData[768], 184);

        digitalWrite(MEM_CS_PIN, HIGH);

        delay(5);
      }
    }
  } else {
    while (1) {
      uint8_t fifoEntries;

      int status = readByte(MEM_CS_PIN, 0x05);
      while (status & 0x01) {
        status = readByte(MEM_CS_PIN, 0x05);
      }

      // Get the number of entries in the memory
      digitalWrite(MEM_CS_PIN, LOW);
      SPI.transfer(0x03);
      SPI.transfer(0x00);
      SPI.transfer(0x00);
      SPI.transfer(0x00);
      fifoEntries = SPI.transfer16(0x00);
      digitalWrite(MEM_CS_PIN, HIGH);

      // Grab all the information in the one continuous read
      address = 0x100;
      while(1) {
        // Read the first data block
        addressTemp = address >> 16;
        // Write to the first free block for the next entry block
        digitalWrite(MEM_CS_PIN, LOW);
        SPI.transfer(0x03);
        SPI.transfer((uint8_t)addressTemp);
        addressTemp = address >> 8;
        SPI.transfer((uint8_t)addressTemp);
        addressTemp = address;
        SPI.transfer((uint8_t)addressTemp);

        uint16_t temp;
        bool brk = false;
        int k = 0;
        for (int j = 0; j < 476; ++j) {
          temp = SPI.transfer16(0x00);
          // Serial.println(temp);
          fifoData[k++] = temp >> 8;
          fifoData[k++] = temp;
        }

        digitalWrite(MEM_CS_PIN, HIGH);

        address += 0x400;
        Serial.println("\n\n");
        // Print what was read
        int j = 0;
        for (int i = 0; i < 136; i++) {
          uint8_t t = fifoData[j++];
          int16_t d;
          if ((t & 0xF8) == 16) {
            // Serial.print("  ");
            Serial.print(t, DEC);
            Serial.print("  ");
            d = (fifoData[j++] << 8) | fifoData[j++];
            Serial.print((d * 0.061 * 9.80665 / 1000) * 0.101971621, DEC);
            Serial.print("  ");
            d = (fifoData[j++] << 8) | fifoData[j++];
            Serial.print((d * 0.061 * 9.80665 / 1000) * 0.101971621, DEC);
            Serial.print("  ");
            d = (fifoData[j++] << 8) | fifoData[j++];
            Serial.print((d * 0.061 * 9.80665 / 1000) * 0.101971621, DEC);
            // Serial.print(" g");
            Serial.print("\r\n   ");
          } else if ((t & 0xF8) == 32) {
            uint32_t time = 0;
            Serial.print(t, DEC);
            Serial.print("  ");
            time = ((fifoData[j + 2] << 24) | (fifoData[j + 3] << 16) | (fifoData[j] << 8) | fifoData[j + 1]);
            j += 6;
            Serial.print(time, DEC);
            Serial.print("\r\n   ");
            // Serial.print(" us\r\n");
          } else if((t & 0xF8) == 8) {
            Serial.print(t, DEC);
            Serial.print("  ");
            d = (fifoData[j++] << 8) | fifoData[j++];
            Serial.print((d * 0.017453293 * 8.75 / 1000) * 57.2958, DEC);
            Serial.print("  ");
            d = (fifoData[j++] << 8) | fifoData[j++];
            Serial.print((d * 0.017453293 * 8.75 / 1000) * 57.2958, DEC);
            Serial.print("  ");
            d = (fifoData[j++] << 8) | fifoData[j++];
            Serial.print((d * 0.017453293 * 8.75 / 1000) * 57.2958, DEC);
            // Serial.print(" deg/s");
            Serial.print("\r\n   ");
          } else {
            // Serial.println(fifoData[j]);
            Serial.println(" ");
            if (fifoData[j] == 0xFF && fifoData[j + 1] == 0xFF && fifoData[j + 2] == 0xFF && fifoData[j + 3] == 0xFF && fifoData[j + 4] == 0xFF && fifoData[j + 5] == 0xFF && fifoData[j + 6] == 0xFF) {
              brk = true;
              break;
            }

            j += 6;
          }
        }

        if (brk == true) {
          Serial.println("DONE");
          break;
        }
      }
      for (;;);
    }
  }
}



void initSPI() {
  SPI.begin();
  SPI.beginTransaction(SPISettings(10000000, MSBFIRST, SPI_MODE0));

  pinMode(SPI_SCK_PIN, OUTPUT);
  digitalWrite(SPI_SCK_PIN, LOW);

  pinMode(SPI_MOSI_PIN, OUTPUT);
  digitalWrite(SPI_MOSI_PIN, HIGH);

  pinMode(SPI_MISO_PIN, INPUT);
}

void writeCommand(int cs, uint8_t command) {
  digitalWrite(cs, LOW);
  SPI.transfer(command);
  digitalWrite(cs, HIGH);
}

void writeByte(int cs, uint16_t data) {
  digitalWrite(cs, LOW);
  SPI.transfer16(data);
  digitalWrite(cs, HIGH);
}

uint8_t readByte(int cs, uint8_t addr) {
  uint8_t result = 0;
  digitalWrite(cs, LOW);
  SPI.transfer(addr);
  result = SPI.transfer(0x00);
  digitalWrite(cs, HIGH);
  return result;
}

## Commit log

2022-05-05 SolidWorks Added
    [MotorAssy.SLDASM, MotorModel.SLDPRT, MotorMount.SLDPRT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]
2022-05-05 Create imu subsystem
2022-05-05 Added pictures and updated readme
    [MotorAssy.SLDASM, MotorModel.SLDPRT, MotorMount.SLDPRT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]
2022-09-17 Added BOM info
    [billOfMaterials.xlsx]
2022-11-09 switched folder
2022-11-29 Power Subsystem additions
2022-11-29 Added poster and final BOM
    [billOfMaterials.xlsx]
2022-11-29 Updated PCB and software
    [Capstone.kicad_pcb, Capstone.kicad_sch, Capstone.step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]
2022-11-29 moved some pics
    [Battery Carrier.SLDPRT, PCB Carrier.SLDPRT]
2022-12-01 added motor controller subsystem and probe casing subsystem
    [ProbeCasingAssy.SLDASM]

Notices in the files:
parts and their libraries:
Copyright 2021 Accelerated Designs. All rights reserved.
